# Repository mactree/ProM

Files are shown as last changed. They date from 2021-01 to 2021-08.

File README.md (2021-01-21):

# ProM Espresso Display
Ersatz für das kaputte Display

### Kommunikation Display / Hauptplatine
Die Kommunikation erfolgt über die serielle Schnittstelle mit 19200Baut.
Das Signal ist invertiert.

### Funktion 
im Speicher des µC auf der Hauptpaltine ist keine Zeit gespeichert. Diese wird vom Display angefordert. Sendet das Display eine Zeit, kann diese "abgemahlen" werden. Ist die Zeit auf Null wird sie erneut vom Display angefordert.

Läuft die Mühle, sendet die Hauptplatine die aktuelle Zeit an das Display.

### Paket von der Hauptplatine
Vom µC der Hauptpaltine werden 9 byte in einem Paket gesendet.
Nach dem vom Display eine Antwort gesendet wurde, wird das nächste Paket gesendet.

Bsp:
'240','6','6','164','0','71','113','0','168'

#### Bedeutung der Zeichen (bytes)

1. Bedeutung: unklar / konstant: ja / Wert: '240'

2. Bedeutung: unklar / konstant: ja / Wert: '6'

3. Bedeutung: unklar / konstant: ja / Wert: '6'

4. Bedeutung: Status / konstant: nein / bekannte Werte:
   	'164' Siebträgertaster nicht gedrückt

   	'167' Siebträgertaster gedrückt => Mühle läuft

   	'165' Timer abgelaufen / Siebträgertaster immernoch gedrückt

   	'160' neue Zeit anfordern

5. Bedeutung: unklar / konstant: ja / Wert: '0'

6. Bedeutung: unklar / konstant: nein / bekannte Werte: '0', '71', '73'

7.  Bedeutung: Bestandteil der Zeit / konstant: nein / bekannte Werte '0' - '254' 

8. Bedeutung: Bestandteil der Zeit / konstant: nein / bekannte Werte '0' - '254' 

9. Bedeutung: unklar / konstant: nein / bekannte Werte: 

#### Berechnung der Zeit
Die maximal einstellbare Zeit der ProM beträgt 18s.

Nimmt man den Binärwert von **byte8** und **byte7** und konvertiert die 16bit in den Dezimalwert 

**Bsp:**

byte8: '3'	bin: 00000011

byte7: '231' bin: 11100111

byte8 &byte7: 0000001111100111 => dec: 999

Multipliziert man den Wert mit **0,018** erhält man **17,982** => eingestellt waren 18s

### Paket vom Timer

Als Antwort sendet das Display ein Paket aus vier bytes:
'240','1','6','9'

#### Bedeutung der Zeichen (bytes)
1. Bedeutung: unklar / konstant: ja / Wert: '240'
2. Bedeutung: unklar / konstant: ja / Wert: '1'
3. Bedeutung: unklar / konstant: ja / Wert: '6'
4. Bedeutung: unklar / konstant: ja / Wert: '9'

Fordert die Hauptplatine eine Zeit vom Display an, so wird diese in einem Paket aus 9 bytes gesendet. 
**'240','6','12','1','0','0','231','3','19'**

#### Bedeutung der Zeichen (bytes)
1. Bedeutung: unklar / konstant: ja / Wert: '240'
2. Bedeutung: unklar / konstant: ja / Wert: '6'
3. Bedeutung: unklar / konstant: ja / Wert: '12'
4. Bedeutung: unklar / konstant: nein / Wert: '1'
5. Bedeutung: unklar / konstant: ja / Wert: '0'
6. Bedeutung: unklar / konstant: ja / Wert: '0'
7. Bedeutung: Bestandteil der Zeit / konstant: nein / bekannte Werte '0' - '254' 
8. Bedeutung: Bestandteil der Zeit / konstant: nein / bekannte Werte '0' - '254' 
9. Bedeutung: Prüfsumme / konstant:nein / Wert: byte9 = 254 - (byte4 + byte5 + byte6 + byte7 + byte8)

## Beispielcode
der Code verwendet Softserial, hiermit lässt sich das Signal invertieren.

Beim Start des Codes wird eine Zeit an die Hauptplatine gesendet, diese Zeit kann dann "abgemahlen" werden.

Über den Serial-Monitor wird die Zeit ausgegeben.

### Ziele
Als Display wird ein 1,8 zoll tft mit ST7735 Chip angestrebt.
3 Buttons 'Minus' | 'Timer/ Setup' | 'Plus'

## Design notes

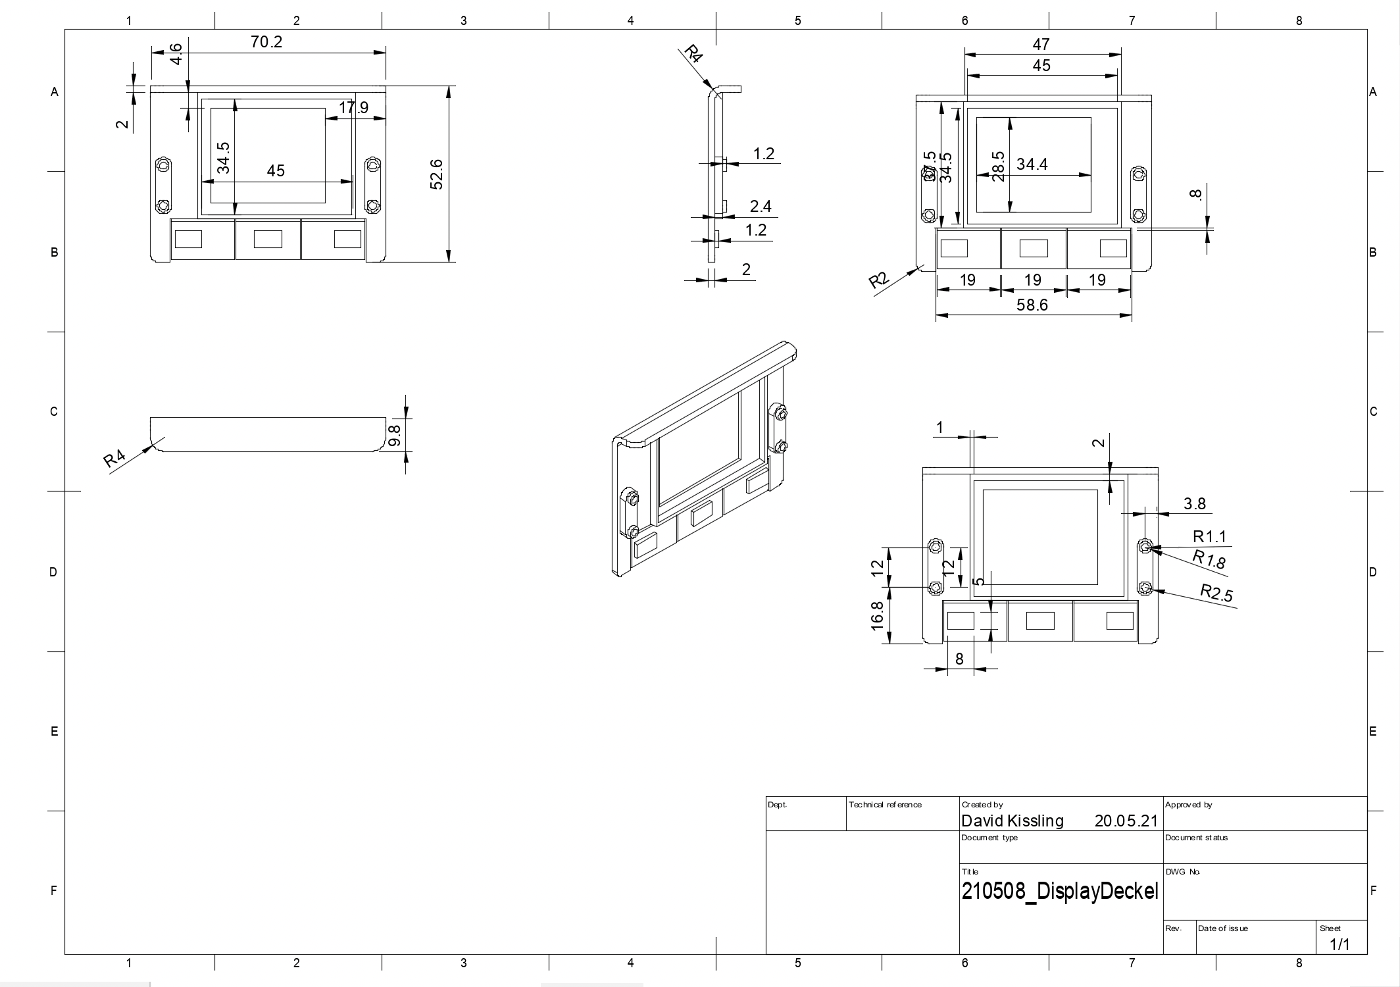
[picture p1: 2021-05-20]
Displayschale/Display Front.png

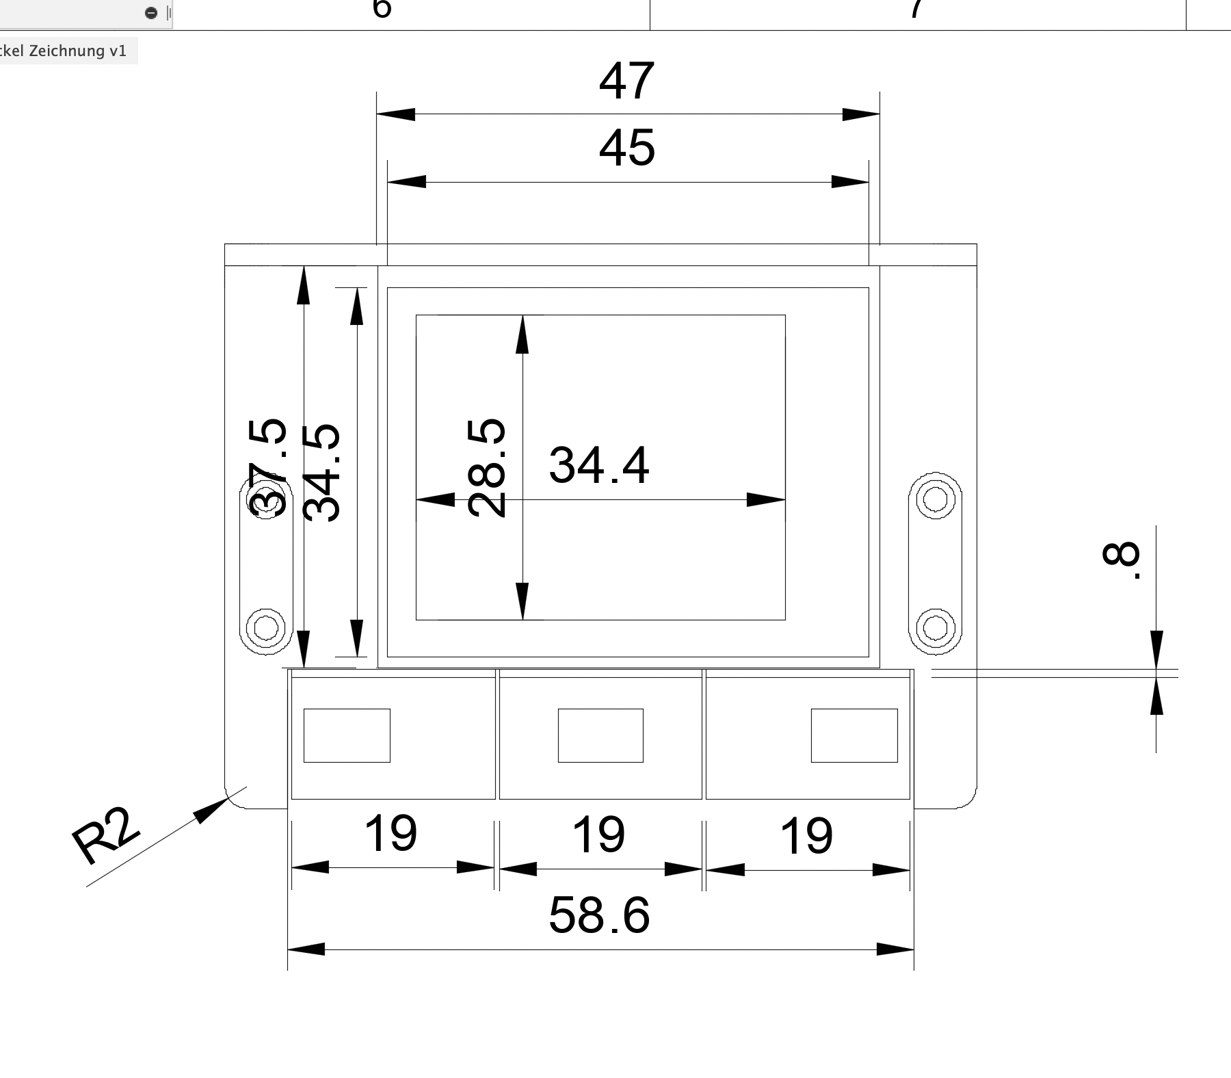
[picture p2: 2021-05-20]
Displayschale/Display Front Detail.png

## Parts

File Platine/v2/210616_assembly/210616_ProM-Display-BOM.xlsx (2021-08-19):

Designator | Quantity | Value | Footprint | LCSC Part #
C1 C2 | 2 | 10¬µF | 1206 | C13585
C3 C4 | 2 | 12p | 0402 | C1547
C5 C6 C7 C8 C9 C10 C11 C12 C13 | 9 | 100nf | 0402 | C1525
D1 | 1 | B581W | SOD-123 | C8598
FB1 | 1 | 100 @ 100 MHz | 0805 | C1015
Q1 | 1 | Q_NPN_BEC | SOT-23-3 | C2146
R1 R2 R3 R4 R5 | 5 | 2.2KŒ© | 0402 | C25879
R6 R7 R8 R9 R10 | 5 | 3.3KŒ© | 0402 | C25890
R11 | 1 | R_Small | 0402 | C25744
R12 | 1 | 1KŒ© | 0402 | C11702
R13 | 1 | 10KŒ© | 0402 | C25744
R14 | 1 | 10Œ© | 0603 | C22859
U1 | 1 | ATmega328P-AU | TQFP-32_7.0x7.0x0.8P | C14877
U2 | 1 | AMS1117-3.3 | SOT-223 | C6186
U3 | 1 | MAX3232 | HTSSOP-16_EP_4.4x5.0x0.65P | C13482
Y1 | 1 | Crystal_GND24_Small | SMD-CRY-3225_4P | C13738

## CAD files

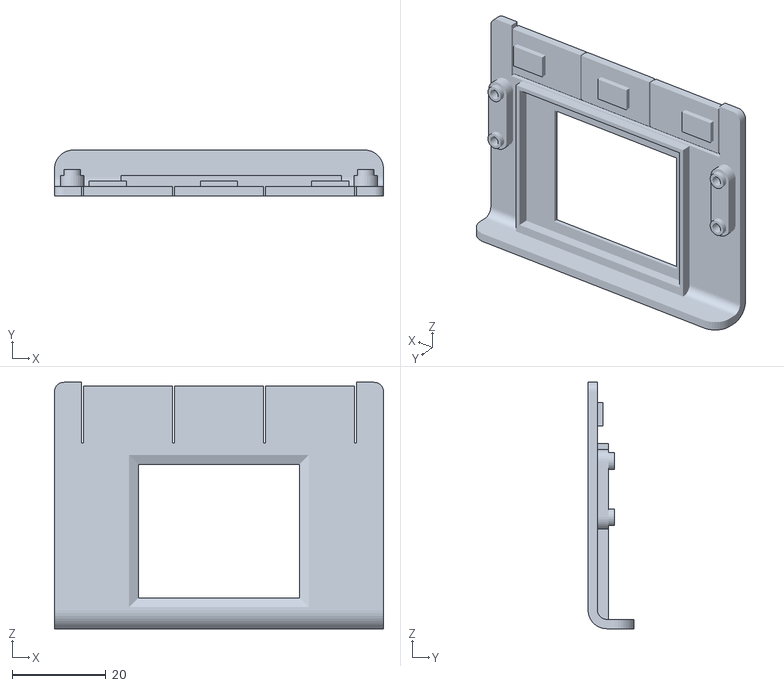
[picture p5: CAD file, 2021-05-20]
Displayschale/210513_ProM-Display.stl
70.2 x 9.80 x 52.6

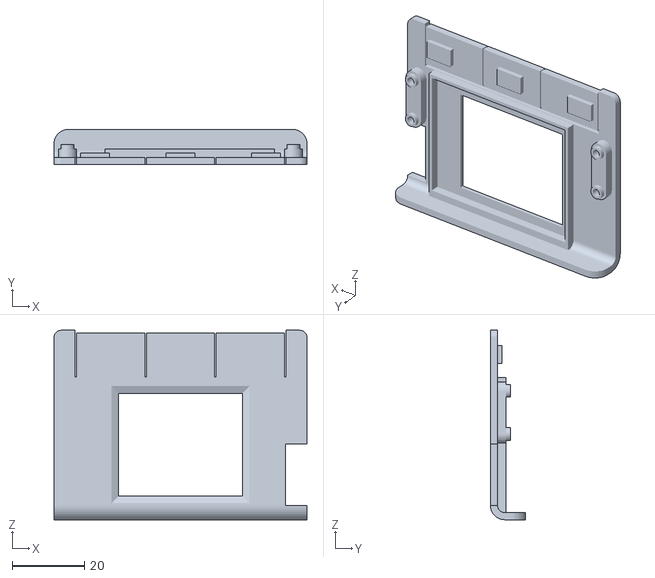
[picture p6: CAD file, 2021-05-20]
Displayschale/210509-DisplayDeckel_pro.stl
70.2 x 9.80 x 52.6

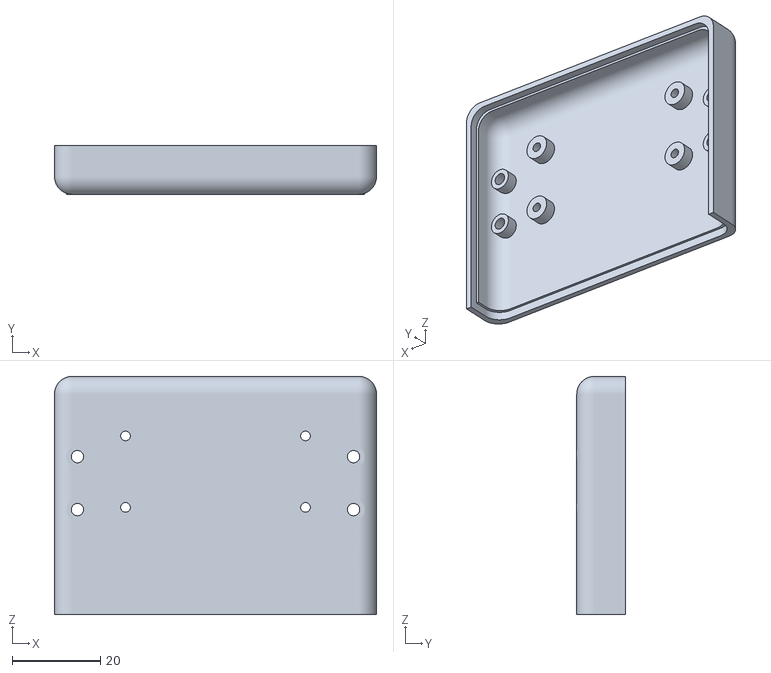
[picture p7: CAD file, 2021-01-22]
Displayschale/201017 Schale.stl
73.0 x 11.0 x 54.0

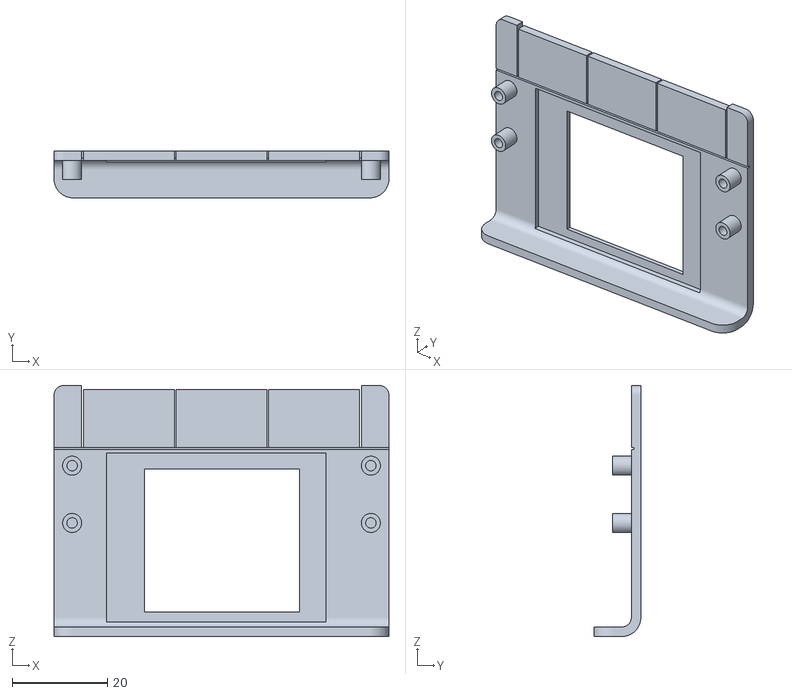
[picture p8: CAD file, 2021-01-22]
Displayschale/201019-4 Front.stl
70.2 x 9.80 x 52.6

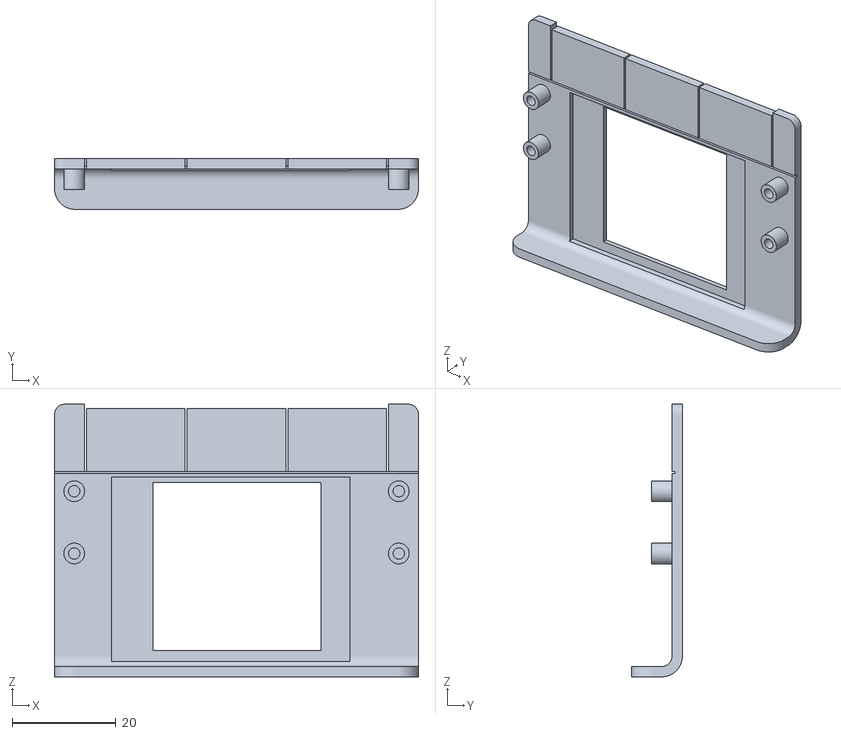
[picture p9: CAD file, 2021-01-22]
Displayschale/201019-3 Front.stl
70.2 x 9.80 x 52.6

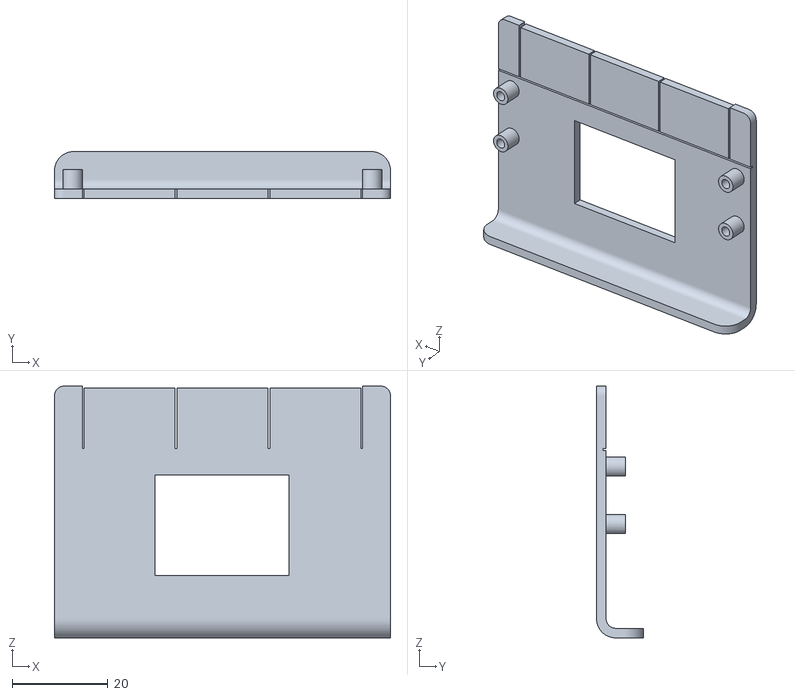
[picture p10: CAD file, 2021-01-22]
Displayschale/201018-2 Front.stl
70.2 x 9.80 x 52.6

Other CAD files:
Displayschale/201018-1 Front.stl
Displayschale/201018 Front.stl
Displayschale/201018 Schale.stl
Displayschale/_Archiv/201018 Front.stl
Displayschale/_Archiv/201018 Schale.stl
Displayschale/_Archiv/201018-1 Front.stl
Displayschale/ProM Display Halter v12.f3d

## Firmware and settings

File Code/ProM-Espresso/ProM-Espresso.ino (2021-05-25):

#include <EEPROM.h>
#include <TFT_ST7735.h> // Graphics and font library for ILI9341 driver chip
#include <SPI.h>

#include "graphic.h"

//Display
TFT_ST7735 tft = TFT_ST7735();  // Invoke library, pins defined in User_Setup.h
// 1,8 zoll TFT GND => GND | VCC => 3.3V | SCL => D13 | SDA => D11 | RES => D8 | DC => D9 | CS => D10 | BL => D7
const byte BL_PIN = 7;   // backlight pin
const bool BL_ON = HIGH;    // pin state for acting backlight as ON
const bool BL_OFF = LOW;    // pin state for acting backlight as OFF

// buttons
const byte BTN1 = 3; // Timerselect and Setup
const byte BTN2 = 4; // minus / cup
const byte BTN3 = 2; // plus / double cup

enum { BTN1_NONE = 0, BTN1_SHORTPRESS, BTN1_LONGPRESS };
enum { BTN2_NONE = 0, BTN2_SHORTPRESS, BTN2_LONGPRESS };
enum { BTN3_NONE = 0, BTN3_SHORTPRESS, BTN3_LONGPRESS };

#define LONGPRESS_TIME    2000  // 2s for a long press


// EEPROM
#define EEPROM_VALUE_VERSION   8

#define SETTINGS               0
#define DOSE1                  1 // one cup
#define DOSE2                  2 // double cup
#define DOSE3                  3 // portalfilter manual mode 18s

#define SET1                   1 // cleaning alarm
#define SET2                   2 // counter all
#define SET3                   3 // counter burs
#define SET4                   4 // enable debug



volatile byte menu = DOSE1;
volatile bool updateEpr = false;
volatile byte setting = SET1;

bool inSetupMode = false;
bool inEditMode = false;

int doseTime[] = {0, 310, 520, 1800};
int settingSet[] = {0, 0, 0, 0};

bool updateMenu = true;
bool updateTime = true;
bool updateButtons = true;


bool switchColor = false;
bool hopperOff = false;
bool resetScreen = false;
bool disableButtons = false;

int inData4_now;
int inData4_prev;


// pause grinding inData[3] == 228
unsigned long previousPauseMillis = 0;
unsigned long PausedTime;

// heartbeattimer
unsigned long previousMillis = 0;
const long interval = 50;

// grind counter
unsigned int counterTimer1;
unsigned int counterTimer2;
unsigned int counterTimer3;
unsigned int counterTotal;
unsigned int counterCleaning;

// serial buffer
byte inData[10];
int index = -1;
byte iByte;
float t = 0;

// Debug
bool showDebug = false;

void setup() {

  // start serial
  Serial.begin(19200);

  // setup button 1
  pinMode(BTN1, INPUT);
  digitalWrite(BTN1, HIGH);

  // setup button 2
  pinMode(BTN2, INPUT);
  digitalWrite(BTN2, HIGH);

  // setup button 3
  pinMode(BTN3, INPUT);
  digitalWrite(BTN3, HIGH);

  // setup backlightpin
  pinMode(BL_PIN, OUTPUT);
  digitalWrite(BL_PIN, BL_ON);

  // init display
  tft.init();
  tft.setRotation(3);
  tft.fillScreen(TFT_BLACK);

  // draw version string
  tft.setTextColor( TFT_BLUE, TFT_BLACK);
  tft.drawString("v102.105.025", 40, 80, 2);
  delay(1000);
  tft.fillScreen(TFT_BLACK);

  // read settings
  readSettings();

  // send time
  sendTime();

}

void loop() {

  // handle buttons
  byte btn1Event = handleButton1();
  byte btn2Event = handleButton2();
  byte btn3Event = handleButton3();


  // shortpress
  if (btn1Event == BTN1_SHORTPRESS && !disableButtons) {
    btn1();
  }
  // shortpress btn1 while inEditMode
  else if (btn1Event == BTN1_SHORTPRESS && inEditMode) {
    handleEditMode();
  }

  // shortpress cup
  //  else if(btn2Event == BTN2_SHORTPRESS && inData[3] == (164)){
  else if (btn2Event == BTN2_SHORTPRESS  && !disableButtons) {
    btn2();
  }
  // shortpress double cup
  //  else if(btn3Event == BTN3_SHORTPRESS && inData[3] == (164){
  else if (btn3Event == BTN3_SHORTPRESS && !disableButtons) {
    btn3();
  }
  // longpress cup or double cup
  else if (((menu == 1 && btn2Event == BTN2_LONGPRESS) || (menu == 2 && btn3Event == BTN3_LONGPRESS)) && !disableButtons) {
    handleEditMode();
  }
  // longpress cup or double cup
  else if ((btn1Event == BTN1_LONGPRESS)  && !disableButtons) {
    showDebug = !showDebug;
    updateMenu = true;
  }
  readSerial();

  tftShow();

  sendHeartbeat();

  grinderStatus();

}

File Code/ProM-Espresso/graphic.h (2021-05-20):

#include <avr/pgmspace.h>

#define cup_width 60
#define cup_height 46
const unsigned char cup [] PROGMEM = {
0x0,0x0,0x0,0x0,0x0,0x0,0x0,0x0,
0x7f,0xff,0xff,0xff,0xff,0xfc,0x0,0x0,
0xff,0xff,0xff,0xff,0xff,0xfc,0x0,0x0,
0xc0,0x0,0x0,0x0,0x0,0xc,0x38,0x0,
0xc0,0x0,0x0,0x0,0x0,0xc,0xfe,0x0,
0xc0,0x0,0x0,0x0,0x0,0xf,0x83,0x80,
0xc0,0x0,0x0,0x0,0x0,0xe,0x1,0xc0,
0xc0,0x0,0x0,0x0,0x0,0xc,0x0,0xc0,
0x40,0x0,0x0,0x0,0x0,0xc,0x0,0x60,
0x40,0x0,0x0,0x0,0x0,0xc,0x0,0x60,
0x40,0x0,0x0,0x0,0x0,0xc,0x0,0x60,
0x40,0x0,0x0,0x0,0x0,0xc,0x0,0x60,
0x60,0x0,0x0,0x0,0x0,0xc,0x0,0x60,
0x60,0x0,0x0,0x0,0x0,0x8,0x0,0xc0,
0x60,0x0,0x0,0x0,0x0,0x18,0x1,0xc0,
0x60,0x0,0x0,0x0,0x0,0x18,0x3,0x80,
0x20,0x0,0x0,0x0,0x0,0x18,0x7,0x0,
0x30,0x0,0x0,0x0,0x0,0x18,0xc,0x0,
0x30,0x0,0x0,0x0,0x0,0x30,0x38,0x0,
0x30,0x0,0x0,0x0,0x0,0x30,0x60,0x0,
0x18,0x0,0x0,0x0,0x0,0x31,0xc0,0x0,
0x18,0x0,0x0,0x0,0x0,0x23,0x80,0x0,
0x18,0x0,0x0,0x0,0x0,0x67,0x0,0x0,
0xc,0x0,0x0,0x0,0x0,0x7c,0x0,0x0,
0xc,0x0,0x0,0x0,0x0,0xf8,0x0,0x0,
0x6,0x0,0x0,0x0,0x0,0xf0,0x0,0x0,
0x6,0x0,0x0,0x0,0x0,0xe0,0x0,0x0,
0x6,0x0,0x0,0x0,0x1,0xc0,0x0,0x0,
0x3,0x0,0x0,0x0,0x1,0x80,0x0,0x0,
0x3,0x0,0x0,0x0,0x1,0x80,0x0,0x0,
0x3,0x0,0x0,0x0,0x3,0x0,0x0,0x0,
0x1,0x0,0x0,0x0,0x3,0x0,0x0,0x0,
0x1,0x80,0x0,0x0,0x3,0x0,0x0,0x0,
0x1,0x80,0x0,0x0,0x2,0x0,0x0,0x0,
0x1,0x80,0x0,0x0,0x6,0x0,0x0,0x0,
0x0,0x80,0x0,0x0,0x6,0x0,0x0,0x0,
0x0,0x80,0x0,0x0,0x6,0x0,0x0,0x0,
0x0,0xc0,0x0,0x0,0x6,0x0,0x0,0x0,
0x0,0xc0,0x0,0x0,0x6,0x0,0x0,0x0,
0x0,0xc0,0x0,0x0,0x6,0x0,0x0,0x0,
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
};


#define cup_small_width 18
#define cup_small_height 14
const unsigned char cup_small [] PROGMEM = {
0xff,0xfc,0x0,
0x80,0x7,0x80,
0x80,0x6,0x40,
0x80,0x4,0x40,
0x80,0x4,0x80,
0xc0,0xd,0x0,
0x40,0xa,0x0,
0x40,0xc,0x0,
0x40,0x8,0x0,
0x40,0x8,0x0,
0x60,0x18,0x0,
0x20,0x10,0x0,
0x20,0x10,0x0,
0x3f,0xf0,0x0
};


#define minus_width 14
#define minus_height 14
const unsigned char minus [] PROGMEM = {
0x0,0x0,
0x0,0x0,
0x0,0x0,
0x0,0x0,
0x0,0x0,
0x0,0x0,
0xff,0xfc,
0xff,0xfc,
0x0,0x0,
0x0,0x0,
0x0,0x0,
0x0,0x0,
0x0,0x0,
0x0,0x0
};

#define plus_width 14
#define plus_height 14
const unsigned char plus [] PROGMEM = {
0x3,0x0,
0x3,0x0,
0x3,0x0,
0x3,0x0,
0x3,0x0,
0x3,0x0,
0xff,0xfc,
0xff,0xfc,
0x3,0x0,
0x3,0x0,
0x3,0x0,
0x3,0x0,
0x3,0x0,
0x3,0x0
};

#define cups_width 78
#define cups_height 57
const unsigned char cups [] PROGMEM = {
0x3f,0xff,0xff,0xff,0xff,0xf8,0x0,0x0,0x0,0x0,
0x7f,0xff,0xff,0xff,0xff,0xfc,0x0,0x0,0x0,0x0,
0x40,0x0,0x0,0x0,0x0,0xc,0x0,0x0,0x0,0x0,
0xc0,0x0,0x0,0x0,0x0,0xc,0xfe,0x0,0x0,0x0,
0xc0,0x0,0x0,0x0,0x0,0xf,0xef,0x0,0x0,0x0,
0xc0,0x0,0x0,0x0,0x0,0xf,0x1,0x80,0x0,0x0,
0x40,0x0,0x0,0x0,0x0,0xe,0x0,0xc0,0x0,0x0,
0x40,0x0,0x0,0x0,0x0,0xc,0x0,0xc0,0x0,0x0,
0x40,0x0,0x0,0x0,0x0,0xc,0x0,0x60,0x0,0x0,
0x40,0x0,0x0,0x0,0x0,0xc,0x0,0x60,0x0,0x0,
0x40,0x0,0x0,0x0,0x0,0xc,0x0,0x60,0x0,0x0,
0x60,0x0,0x0,0x0,0x0,0xc,0x0,0x60,0x0,0x0,
0x60,0x0,0xf,0xff,0xff,0xff,0xff,0xfe,0x0,0x0,
0x60,0x0,0x1f,0xff,0xff,0xff,0xff,0xff,0x0,0x0,
0x60,0x0,0x18,0x0,0x0,0x0,0x0,0x3,0x0,0x0,
0x20,0x0,0x10,0x0,0x0,0x0,0x0,0x1,0x3f,0x80,
0x30,0x0,0x10,0x0,0x0,0x0,0x0,0x1,0xf9,0xe0,
0x30,0x0,0x10,0x0,0x0,0x0,0x0,0x1,0xc0,0x70,
0x30,0x0,0x10,0x0,0x0,0x0,0x0,0x3,0x80,0x30,
0x10,0x0,0x18,0x0,0x0,0x0,0x0,0x3,0x0,0x18,
0x18,0x0,0x18,0x0,0x0,0x0,0x0,0x3,0x0,0x18,
0x18,0x0,0x18,0x0,0x0,0x0,0x0,0x3,0x0,0x18,
0x18,0x0,0x18,0x0,0x0,0x0,0x0,0x3,0x0,0x18,
0xc,0x0,0x18,0x0,0x0,0x0,0x0,0x3,0x0,0x18,
0xc,0x0,0x18,0x0,0x0,0x0,0x0,0x3,0x0,0x18,
0x6,0x0,0x8,0x0,0x0,0x0,0x0,0x3,0x0,0x30,
0x6,0x0,0x8,0x0,0x0,0x0,0x0,0x2,0x0,0x70,
0x6,0x0,0xc,0x0,0x0,0x0,0x0,0x6,0x0,0xe0,
0x3,0x0,0xc,0x0,0x0,0x0,0x0,0x6,0x3,0xc0,
0x3,0x0,0xc,0x0,0x0,0x0,0x0,0x6,0x7,0x0,
0x3,0x0,0x4,0x0,0x0,0x0,0x0,0x6,0xe,0x0,
0x1,0x0,0x6,0x0,0x0,0x0,0x0,0xc,0x38,0x0,
0x1,0x80,0x6,0x0,0x0,0x0,0x0,0xc,0x70,0x0,
0x1,0x80,0x6,0x0,0x0,0x0,0x0,0xc,0xe0,0x0,
0x1,0x80,0x3,0x0,0x0,0x0,0x0,0x19,0x80,0x0,
0x0,0x80,0x3,0x0,0x0,0x0,0x0,0x1f,0x0,0x0,
0x0,0x80,0x1,0x80,0x0,0x0,0x0,0x1e,0x0,0x0,
0x0,0xc0,0x1,0x80,0x0,0x0,0x0,0x3c,0x0,0x0,
0x0,0xc0,0x1,0x80,0x0,0x0,0x0,0x38,0x0,0x0,
0x0,0xc0,0x0,0xc0,0x0,0x0,0x0,0x70,0x0,0x0,
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
};


#define cups_small_width 21
#define cups_small_height 17
const unsigned char cups_small [] PROGMEM = {
0xff,0xfc,0x0,
0x80,0x7,0x80,
0x80,0x6,0x40,
0x9f,0xff,0x80,
0x90,0x0,0xf0,
0xd0,0x0,0xc8,
0x50,0x0,0x88,
0x50,0x0,0x90,
0x58,0x1,0xa0,
0x48,0x1,0x40,
0x68,0x1,0x80,
0x28,0x1,0x0,
0x28,0x1,0x0,
0x3c,0x3,0x0,
0x4,0x2,0x0,
0x4,0x2,0x0,
0x7,0xfe,0x0
};


#define portalfilter_width 100
#define portalfilter_height 25
const unsigned char portalfilter [] PROGMEM = {
0x0,0x0,0x0,0x0,0x0,0x0,0x0,0x0,0x0,0x0,0x0,0x0,0x0,
0xff,0xff,0xff,0xff,0xe0,0x0,0x0,0x0,0x0,0x0,0x0,0x0,0x0,
0xc0,0x0,0x0,0x0,0x60,0x0,0x0,0x0,0x0,0x0,0x0,0x0,0x0,
0xc0,0x0,0x0,0x0,0x60,0x0,0x0,0x0,0x0,0x0,0x0,0x0,0x0,
0xc0,0x0,0x0,0x0,0x60,0x0,0x0,0x0,0x0,0x0,0x0,0x0,0x0,
0xc0,0x0,0x0,0x0,0x60,0x0,0x0,0x0,0x0,0x3,0xff,0xff,0xc0,
0x40,0x0,0x0,0x0,0x60,0x0,0x0,0x7f,0xff,0xff,0xff,0xf9,0xe0,
0x60,0x0,0x0,0x0,0x63,0xc7,0xff,0xff,0xff,0xc0,0x0,0x0,0x60,
0x60,0x0,0x0,0x0,0x7f,0xe7,0xf8,0x0,0x0,0x0,0x0,0x0,0x30,
0x60,0x0,0x0,0x0,0x0,0x64,0x0,0x0,0x0,0x0,0x0,0x0,0x30,
0x30,0x0,0x0,0x0,0x0,0x64,0x0,0x0,0x0,0x0,0x0,0x0,0x30,
0x30,0x0,0x0,0x0,0x0,0x64,0x0,0x0,0x0,0x0,0x0,0x0,0x30,
0x18,0x0,0x0,0x0,0x0,0x64,0x0,0x0,0x0,0x0,0x0,0x0,0x30,
0x1f,0xff,0xff,0xff,0x0,0x64,0x0,0x0,0x0,0x0,0x0,0x0,0x30,
0xf,0xff,0xff,0xff,0xc0,0x64,0x0,0x0,0x0,0x0,0x0,0x0,0x30,
0x0,0xf,0xfe,0x0,0xf0,0x64,0x0,0x0,0x0,0x0,0x0,0x0,0x30,
0x0,0x1e,0xf,0x0,0x3e,0x64,0x0,0x0,0x0,0x0,0x0,0x0,0x30,
0x0,0x38,0x3,0x80,0x7,0xe6,0x0,0x0,0x0,0x0,0x0,0x0,0x30,
0x0,0x60,0x1,0xc0,0x1,0xe7,0xff,0xff,0xf0,0x0,0x0,0x0,0x60,
0x0,0xe0,0x0,0xc0,0x0,0x0,0x7f,0xff,0xff,0xff,0xff,0x0,0xe0,
0x0,0xc3,0xf0,0x60,0x0,0x0,0x0,0x0,0x0,0xff,0xff,0xff,0xc0,
0x1,0x87,0x38,0x60,0x0,0x0,0x0,0x0,0x0,0x0,0x0,0x3,0x0,
0x1,0x86,0xc,0x60,0x0,0x0,0x0,0x0,0x0,0x0,0x0,0x0,0x0,
0x1,0xfc,0xf,0xe0,0x0,0x0,0x0,0x0,0x0,0x0,0x0,0x0,0x0,
0x1,0xfc,0x7,0xe0,0x0,0x0,0x0,0x0,0x0,0x0,0x0,0x0,0x0
};
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

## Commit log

2021-01-22 Displayschale, tftcode
    [201017 Schale.stl, 201018 Front.stl, 201018 Schale.stl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]
2021-05-20 new Icons, STL
    [201017 Schale.stl, 201018 Front.stl, 201018 Schale.stl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]
2021-05-22 Hopper
    * added Hopper off detection
    * disable buttons on various conditions
2021-05-25 pause reset
    reseting a paused grind after 20s
    [ProM-Espresso.ino, grinder_status.ino, read_Settings.ino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]
2021-05-29 new gerber
    fixed
2021-08-19 pcb v2 files
    [210616_ProM-Display-BOM.xlsx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]
